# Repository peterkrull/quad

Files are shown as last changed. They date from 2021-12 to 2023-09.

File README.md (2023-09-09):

# Project quad

This git repository is a personal project of mine to develop an open-source autonomous quad copter using cheap off-the-shelf components in conjunction with control theory and state estimation. As much as possible, any auxiliary tools and documentation I produce, will also be a part of the repository.

## Getting Rusty

The [firmware](/software/rusty-quad) is written in the Rust programming language. This is in contrast to most flight controllers (and embedded devices in general) which use C or C++. The reason for choosing Rust is quite simple: it is a modern language. It can guarantee many things about the validity of memory at compile time, allows for writing high-level code, that runs at low-level speeds, and feels good to write; once you become friendly with the borrow checker.

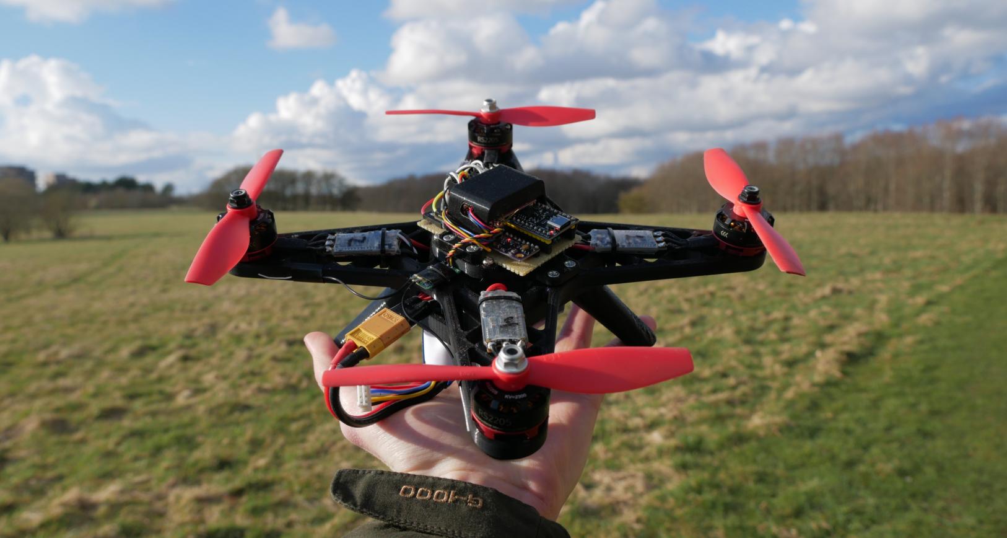
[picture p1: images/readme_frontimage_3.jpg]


### [*YouTube* : Demo of wireless data plotting and responsive controls](https://www.youtube.com/watch?v=jQ53PiUz8Us)

---

## Directory contents

- **[3dparts](/3dparts/)** - 3D models used in the project as STEP and .obj files.
- **[docs](/docs/)** - Documentation and learning material used in the project.
- **[hardware](/hardware/)** - Schematics, and PCB layouts as well as finished gerber files.
- **[images](/images/)** - Photos used in readme and some documentation.
- **[software](/software/)** - Software related to the project, including simulations, firmware, etc.
- **[tests](/tests/)** - Results from test conducted during this project

---

## Related repositories

During this project, some additional tools were developed, that reside in their own repositories.

### Rust crates

- [Async no-std ICM-20948 driver](https://github.com/peterkrull/icm20948-async)
- [Dshot driver for RP2040 PIO](https://github.com/peterkrull/dshot-pio)
- [Magnetometer calibration algorithm](https://github.com/peterkrull/mag-calibrator-rs)
- [Linear multi-sensor Kalman filter](https://github.com/peterkrull/kalman_filter_rust/)
- [(Forked) no-std SBUS-parser](https://github.com/peterkrull/sbus)

---

## License

This work is licensed under GPLv3.

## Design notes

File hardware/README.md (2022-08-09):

# Hardware

While a perfboard-based flight controller is fully capable, it is also heavy, large and labor intensive to manufacture. A compact and integrated PCB is a natural next step to reduce complexity, increase flexibility and reproducability.

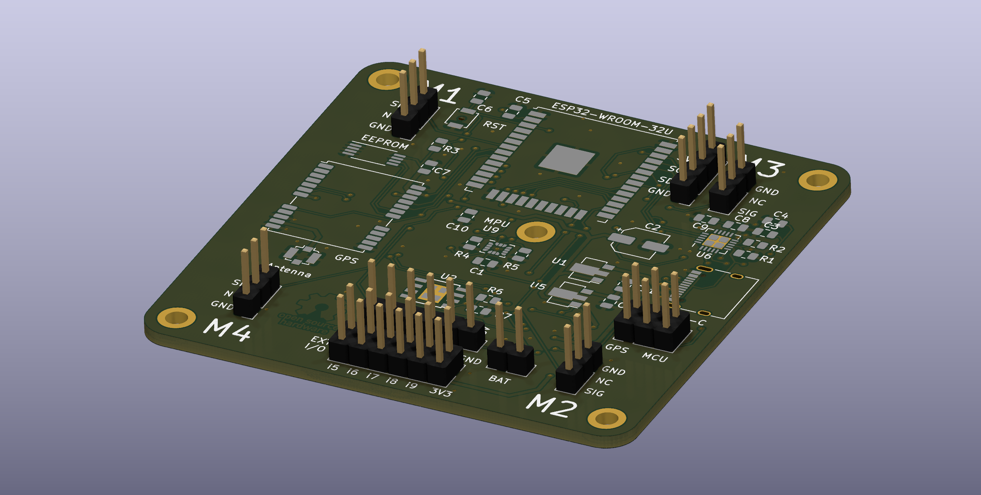
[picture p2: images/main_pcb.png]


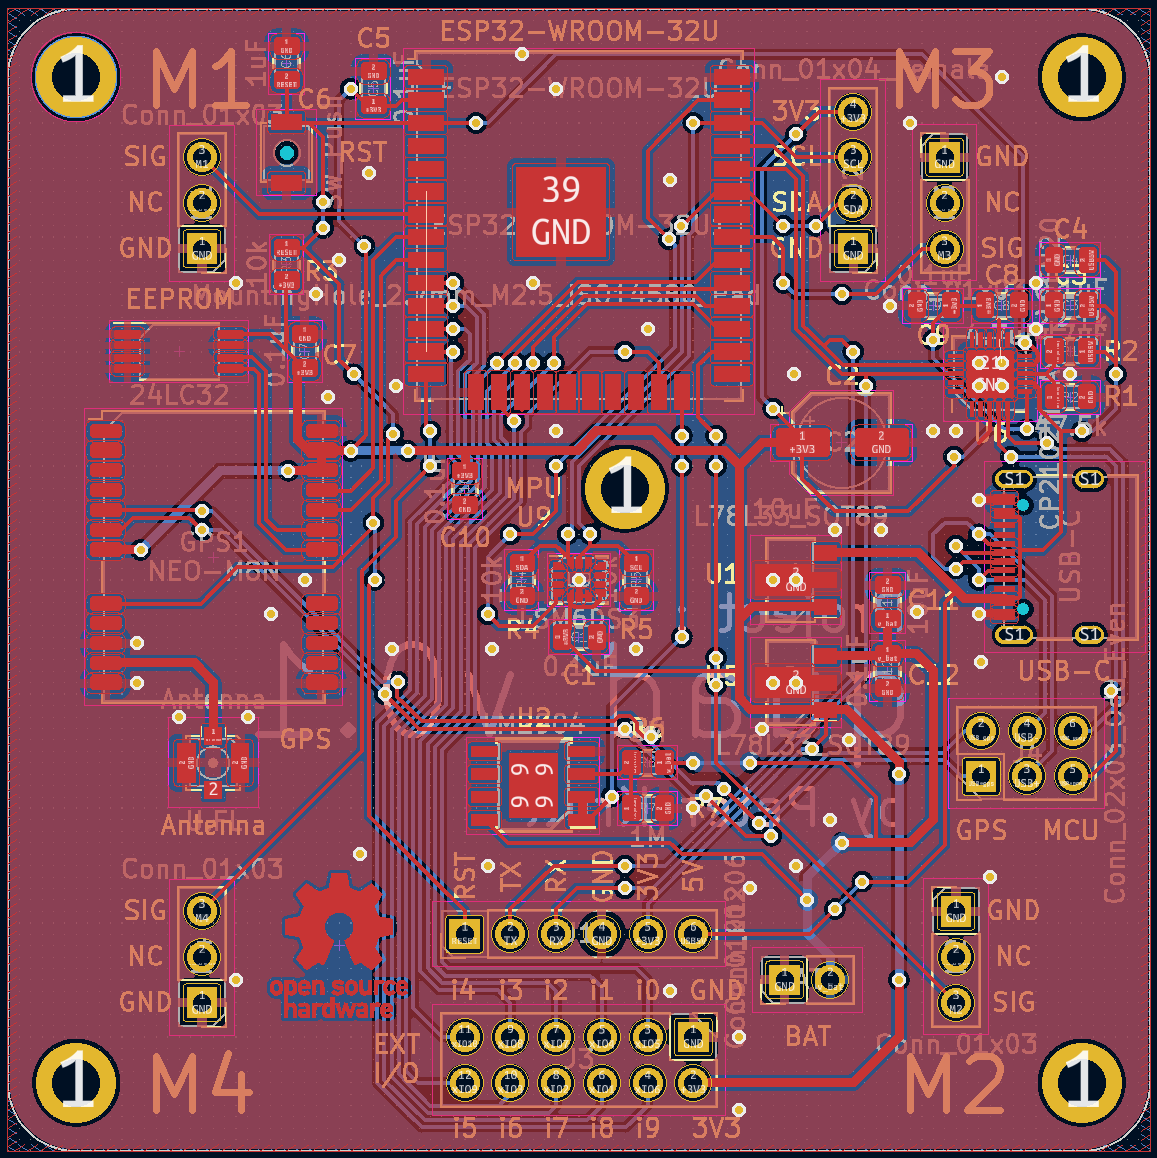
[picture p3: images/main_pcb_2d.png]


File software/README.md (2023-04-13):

# Software design

This directory contains first and foremost the Firmware developed for the drone, as well as any supporting software used for communication and data acquisition, processing, etc.

The rust-based flight controller can be found in
**[rusty-quad](/software/rusty-quad/)**

## Transition from C++ to Rust

The development of the firmware for the drone, has moved from an Arduino (C++) based framework, to Rust. The main micro-controller for development has also transitioned from the ESP32 platform, to the Raspberry Pi Pico (RP2040).

The rust-based firmware, unlike its C++ counterpart, has not yet proven air worthy, since some modules had to be written from scratch. This is due to embedded Rust still being in its infancy.

## Why Rust?

I started experimenting with Rust about a year ago, due to me finding its promises of memory safety, strict (yet somehow incredibly flexible) type system and C-like performance intriguing. On top of that, the modern tooling, package manager and passionate user base had me sold.

Equally intriguing to me, was the prospect of being able to develop micro-controller-embedded applications in Rust, with the amazing [**knurling-rs**](https://knurling.ferrous-systems.com/) tools by Ferrous Systems.

On top of that, Rust allows for high-speed, low overhead asynchronous programs using the built-in async/await syntax. For embedded applications, there is the [**Embassy**](https://github.com/embassy-rs/embassy) project specifically aimed at supporting async on embedded platforms.

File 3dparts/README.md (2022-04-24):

# 3D parts

This directory contains the 3D files designed for this project, both FreeCAD source files and 3D-printable .obj files.

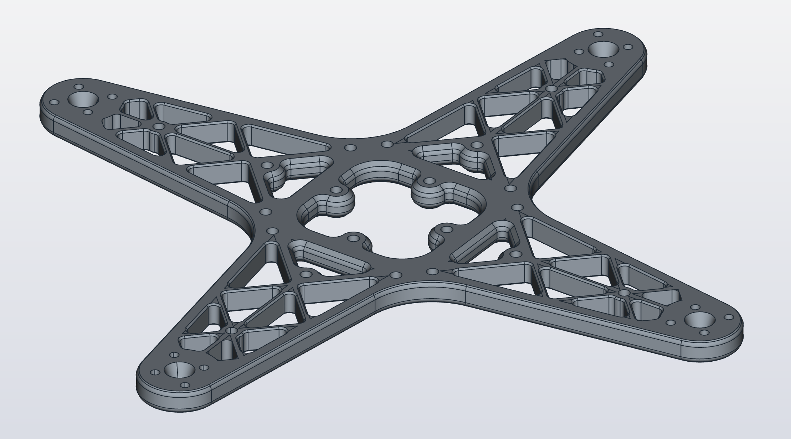
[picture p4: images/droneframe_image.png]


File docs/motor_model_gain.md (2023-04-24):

# Determining the motor model gain

Since the motor model is meant to relate the output thrust in newton to the input Dhsot command, the gain of the transfer function, or the constant in the numerator, is what defines this relation.

---

## Test setup and procedure

The thrust is measured in grams at 50 Hz using a strain gauge of the type [Eilersen SPSX](https://www.eilersen.com/single-point-load-cell/product/single-point-load-cell-spsx/) in combination with the [Eilersen 4X79A](https://www.eilersen.com/analog-weighing-module/product/analog-output-module-4x79a/) digital readout module, connected to a computer via ethernet, and read using a [program](/software/misc-tools/TCP_strain_guage.py) that establishes and logs a TCP data stream. A single motor with propeller is rigidly mounted to the strain gauge using [3D-printed parts](/3dparts/teststand_thrust/) and driven by a 30 A DShot ESC and a 4S Li-Po battery charged to 15.8 V.

---

## Results

Only one test was performed due to time constraints. The data collected using the TCP script mentioned above was imported and processed using a [Julia script](/tests/thrust_response/plotting_thrust_increaser.jl), where the data is converted to the correct units by scaling along both axes, then fitted to a first order polynomial, or a linear function. The resulting plot can be seen below.



Here we are only interested in the slope of the orange function, which is $4.436e-3$. This means that for the motor model, we have:

$$F(s)=\frac{4.436\cdot 10^{-3}}{\tau s + 1}$$

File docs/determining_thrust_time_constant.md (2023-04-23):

# Determining the time constant of a step in thrust

For this test, it is assumed that the thrust come-up of the motor + esc can be approximated as a first order model. Additionally, it is expected that the time constant is the same for any step-increase in thrust, just like the ideal motor model, but this will be verified during the test.

---

## Test setup and procedure

The thrust is measured in grams at 50 Hz using a strain gauge of the type [Eilersen SPSX](https://www.eilersen.com/single-point-load-cell/product/single-point-load-cell-spsx/) in combination with the [Eilersen 4X79A](https://www.eilersen.com/analog-weighing-module/product/analog-output-module-4x79a/) digital readout module, connected to a computer via ethernet, and read using a [program](/software/misc-tools/TCP_strain_guage.py) that establishes and logs a TCP data stream. A single motor with propeller is rigidly mounted to the strain gauge using [3D-printed parts](/3dparts/teststand_thrust/) and driven by a 30 A DShot ESC and a 4S Li-Po battery charged to 15.82 V.

---

## Results

Three tests were performed, where the motor went from a DShot command of 100 to [500](/tests/thrust_response/0500_thrust_response.csv), to [1200](/tests/thrust_response/1200_thrust_response.csv), and finally to [1500](/tests/thrust_response/1500_thrust_response.csv). These are analyzed using a [Julia script](/tests/thrust_response/plotting_thrust_steps.jl), where the step is set to happen at $t = 0$ as well as have steady-state gain of around $1$. An exponential function of the form $F(t)=1-e^{-\frac{t}{\tau}}$ is fitted to the data, where $\tau$ denotes the time constant of the first order system. It is determined for all three tests, that $\tau = 50 \text{ ms}$ is a good fit, striking a middle ground for any deviance there might be between them.



Using the same model in the laplace domain, we can describe the time constant of the motor model:

$$F(s) = \frac{G}{50\cdot 10^{-3}s + 1}$$

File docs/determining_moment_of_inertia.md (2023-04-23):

# Determining roll moment of inertia

The moment of inertia of some object is not always easy to measure. This is especially true if the object is of an odd size, shape and density. But if we are able to treat our object as a 'free body' where all quantities can be accounted for, then we can determine the moment of inertia by doing a test, where the change in angle over time is recorded when we apply a constant torque.

The moment of inertia is determined by applying a constant torque around the axis, and measuring the change in velocity over time. A constant torque can be accomplished using a known mass $M$ hanging by gravity $g$ from a string wound around a cylinder with radius $r$ giving : $\tau_t = M \cdot g \cdot r$. The moment of inertia $J$ can then be found by fitting the measurement to the following model:

A [3D-printed part](/3dparts/droneframe_v1/pitch_bearing_pivot_wide.obj) was designed specifically for this test, that is meant to replace the usual bearing holder for the pitch/roll test stand. This part has a diameter of $35 \text{ mm}$, so $r = (35/2)\cdot 10^{-3}$. Next, i used a roll of electrical tape, weighing $26 \text{ g}$, so $M = 26\cdot 10^{-3}$ and finally $g = 9.82$.

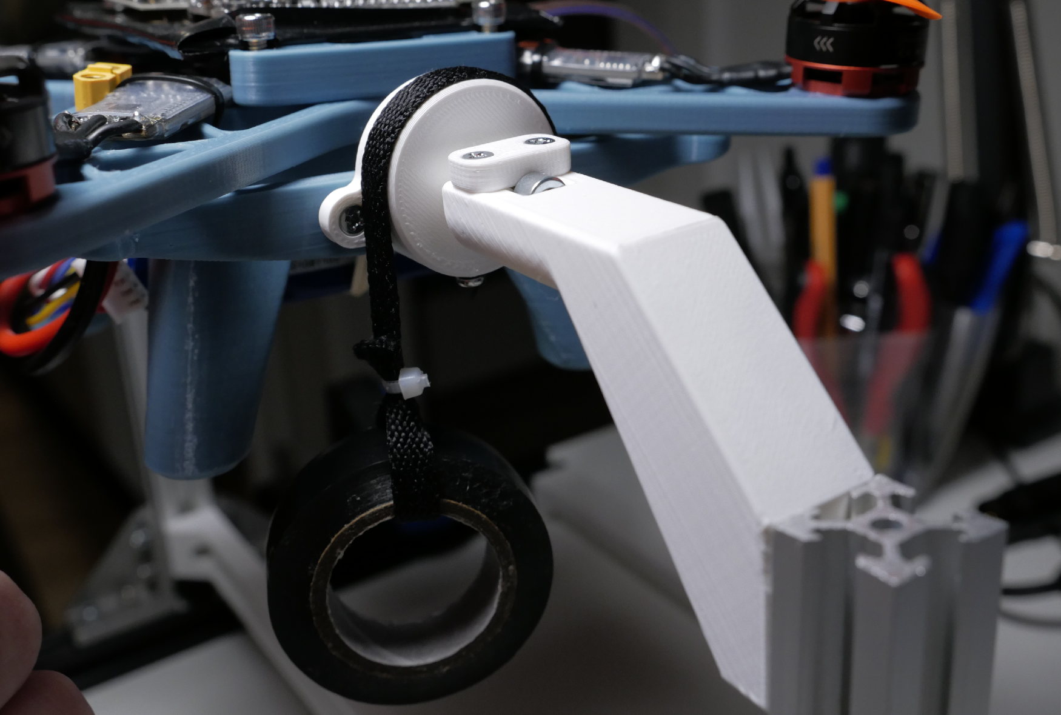
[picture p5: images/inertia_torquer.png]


For the test, a camera was mounted on a tripod recording in 4K with a fast shutter speed to prevent motion blur. Then, the drone was held at an angle to raise the roll of tape up high, and then let go. This is functionally a step in gravity and thus torque, that allows us to observe the change in angle over time. The video is processed in [Physlets tracker](https://physlets.org/tracker/) where two points are tracked on each opposing propeller. This gives us two sets of coordinates ([1](/tests/inertia_meas/pitch_inertia_left_point.csv) and [2](/tests/inertia_meas/pitch_inertia_right_point.csv)), where it is possible to determine the angle between them.

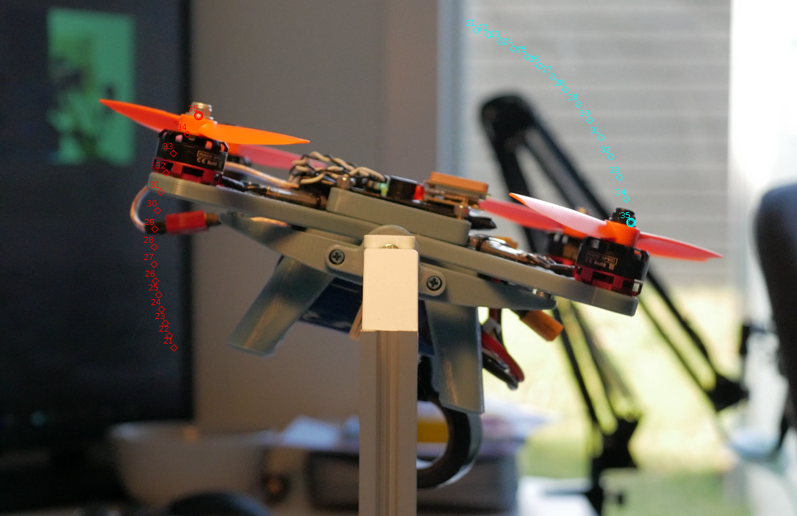
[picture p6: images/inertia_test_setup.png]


Finally, data processing!

A [Julia script](/tests/inertia_meas/roll_moment_inertia.jl) has been developed to calculate the angle using $\texttt{atan2}$, and angular velocity based on the timstamps from the video, as well as determine the moment of inertia that best fits the following transfer function, where some damping $B$ is expected:

$$\omega(s) = \frac{Mgr}{Js} \approx \frac{Mgr}{Js + B}$$

Both the moment of inertia, as well as the damping observed in the test were determined, though the dampening is of limited use at this point.
$$J = 1.2\cdot 10^{-3}$$
$$B = 0.4\cdot 10^{-3}$$



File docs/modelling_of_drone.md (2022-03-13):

# Modelling of drone

For any kind of control system, it is essential to have a good representation of the plant (the system to control) in order to determine the best strategy for control, as well as ensure system stability. For more complex systems, it can be beneficial to determine the transfer functions for smaller components in the system, and then combining them later on. This technique will be utilized here.

---

## Motors

The first critical element of quadcopter dynamics is the motor, propeller and motor controller. It is possible to measure each of these components characteristics individually, but as far as thrust is concerned they are essentially a SISO (single input, single output) system, thus may only be interested in the input/output characteristic. The measurement of step response and results of the motor, propeller and motor controller combo used for this project can be found in the [following document finding the time constant](/docs/determining_thrust_time_constant.md), in combination with [this document finding the gain](/docs/motor_model_gain.md) a first order transfer function can be determined of the form:

$$F(s) = \frac{G}{\tau s+1} \left[\frac{\text{N}}{\text{dshot}}\right]$$

Where $G$ is the steady-state relationship between input dshot command and thrust in newton around the operating point corresponding to a hover. We also have $\tau$ being the time constant of the first order system. The measurements resulted in the following transfer function:

$$F(s) = \frac{4.436\cdot10^{-3}}{50\cdot10^{-3}s+1}$$

---

## Equation of motion for pitch and roll

In [this document](/docs/equations_of_motion_pitch.md) the equation of motion for pitch and roll were determined

$$G(s)= \frac{2D}{Js+B} \left[\frac{\omega}{\text{N}}\right]$$

Where $D$ is the distance from the between two propellers, $J$ is the moment of inertial of the drone around the given axis, and $B$ is the air resistance. Here, $D$ is the only easily measureable constant. 

The moment of inertia is determined by applying a constant torque around the axis, and measuring the change in velocity over time. A constant torque can be accomplished using a known mass $M$ hanging by gravity $g$ from a string wound around a cylinder with radius $r$ giving : $\tau_t = M \cdot g \cdot r$. The moment of inertia $J$ can then be found by fitting the measurement to the following model:

$$\omega(s) = \frac{Mgr}{Js}$$

The value of $J$ for the pitch axis was found during the test described in [this document](/docs/determining_moment_of_inertia.md) to have a value of $1.2\cdot 10^{-3} \text{kg}/\text{m}^2$. A dampening constant $B$ was also found during the test, though this also included friction from the test setup, so the air resistance is approximated as half of this, resulting in the following transfer function for pitch:

$$G(s)= \frac{170\cdot 10^{-3}}{1.2\cdot 10^{-3}s+200\cdot 10^{-6}}$$

The moment of inertia for roll will not be explicitly measured, but it assumed to be $\approx 10$% lower due to the orientation of the battery.

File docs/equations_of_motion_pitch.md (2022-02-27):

# Pitch and roll - Equations of motion

In order to describe the relationship between the thrust of each motor and the roll behaviour, we can utilize a free-body diagram go get a better understanding of the elements at play and how they affect the system. Here we are interested in the mass moment of inertia of the drone, represented by $J$, the force provided by each motor $F_1,F_2,F_3,F_4$, the distance from the motor to the center of mass $R$, and finally the air resistance modelled as a pure dampener $B$

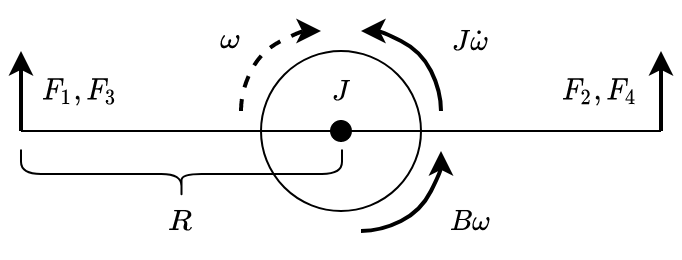
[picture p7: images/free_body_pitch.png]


Using this diagram, we can set up the following equations, considering the direction of rotation denoted by $\omega$.

$$J\dot{\omega} = F_2F_4R-F_1F_3R-B\omega$$

We bring it to the laplace domain:

$$J\omega(s)s = F_2(s)F_4(s)R-F_1(s)F_3(s)R-B\omega(s)$$

Next, we can simplify the motor forces. Since for a clockwise roll command, motors $F_1,F_3$ will increase in thrust, and motors $F_1,F_3$ will decrese with a similar, but negative amount of thrust, we can simplify to:

$$J\omega(s)s = 4F(s)R-B\omega(s)$$

We can now combine terms containing $\omega(s)$

$$\omega(s)(Js+B) = 4F(s)R$$

And finally cross-divide to get the transfer function. Since it might be easier to simply measure the distance between the center of two motors, we can define that $D = 2R$:

$$G(s)=\frac{\omega(s)}{F(s)} = \frac{4R}{(Js+B)} = \frac{2D}{(Js+B)}$$

This transfer function of the first order, due to the single $s$, resulting in a pole. It does assume that the propellers are a point source of thrust, and that they are on the exact same plane as the mass moment of inertia $J$. This might not be the case in reality, but the equation is likely to approximate the forces close enough.

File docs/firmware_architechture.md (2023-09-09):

# Firmware Architechture

This document seeks to describe the high-level design of the [flight controller](/software/rusty-quad/), written in Rust around the [Embassy](https://embassy.dev/) framework. This document will not go into depth with anything specific to the implementation (that is, no Rust code is shown), but the design will rely on some of the syncronization primitives provided by the Embassy framework.

## Message passing

The firmware makes great use of the async functionality provided by Embassy. This includes splitting the logic into a bunch of small self-contained programs, realized via Embassy `tasks`. The firmware therefore also relies heavily on message passing, usually via the `PubSubChannel` type, to allow for multiple receivers of the same message.

The firmware archtechture is described by the the diagram below.

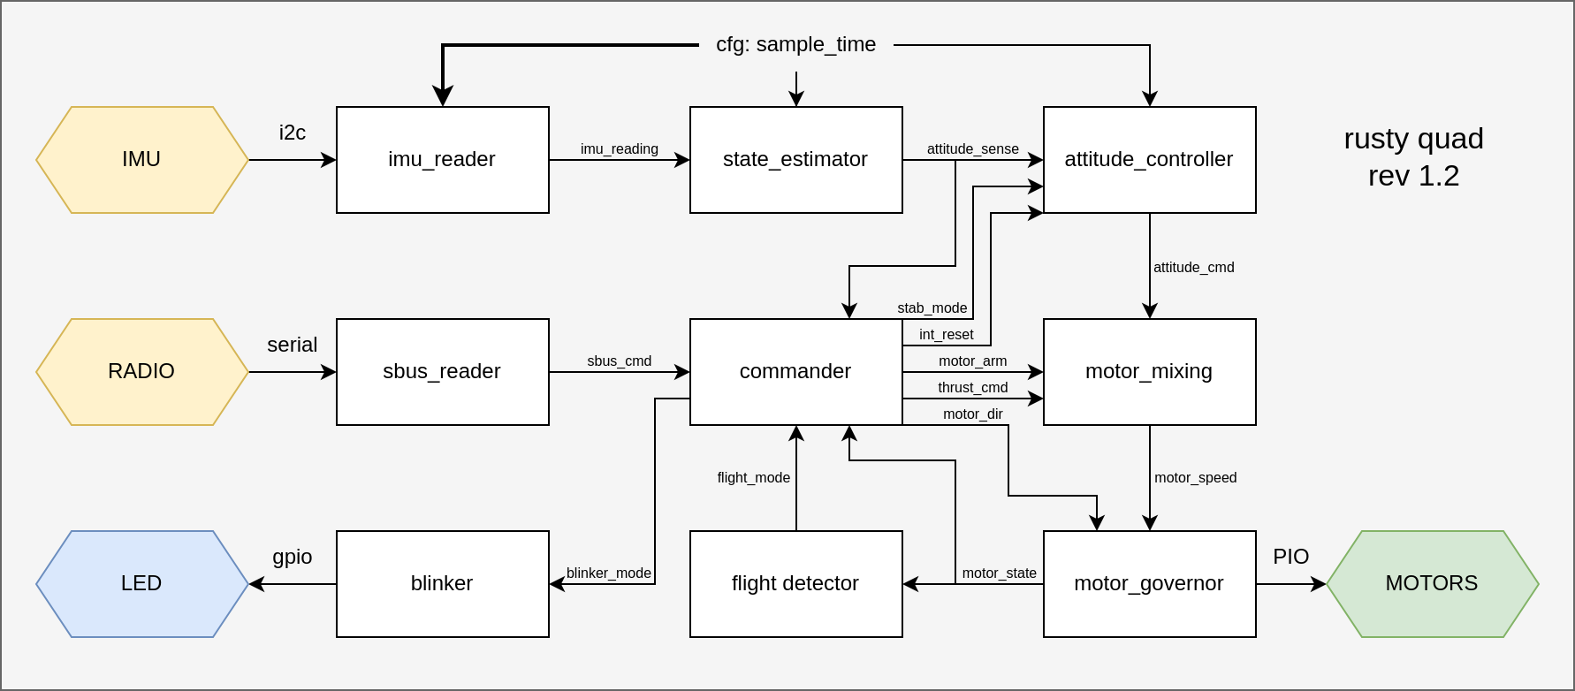
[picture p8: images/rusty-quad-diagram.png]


The architechture is arguably overkill given the current set of functionality, but it should *hopefully* make it easier to add more functionality down the road.

## Task signature structure

Each task signature must follow a clear set of rules, such that input/output relations are more easily reasoned. Take the example signature below. Inputs are clearly listed first, and outputs last. Additionally, the type of the signals are defined in a crate module called `signals`, such that everything relating to these signals, including the type of data and the number of receivers are contained in a single file.

```rust
use crate::signals;

#[embassy_executor::task]
pub async fn controller(
    in_enable:       signals::ConEnableSub,
    in_setpoint:     signals::ConSetpointSub,
    in_measurement:  signals::ConMeasurementSub,
    out_output:      signals::ConOutputPub,
) { ... }
```

The `PubSubChannel` channel type also allows for multiple senders, and queueing of data. These use cases are however not utilized in this project as of yet.

Each signal is defined by the number of receivers (subscribers), as well as the type of data within it. For example, the `ConEnableSub` signal from the example above could be defined like this.

```rust
const CON_ENABLE_NUM: usize = 1;
pub type ConEnableType = bool;
pub type ConEnablePub = Pub<ConEnableType,CON_ENABLE_NUM>;
pub type ConEnableSub = Sub<ConEnableType,CON_ENABLE_NUM>;
pub static CON_ENABLE : Ch<ConEnableType,CON_ENABLE_NUM> = PubSubChannel::new();
```

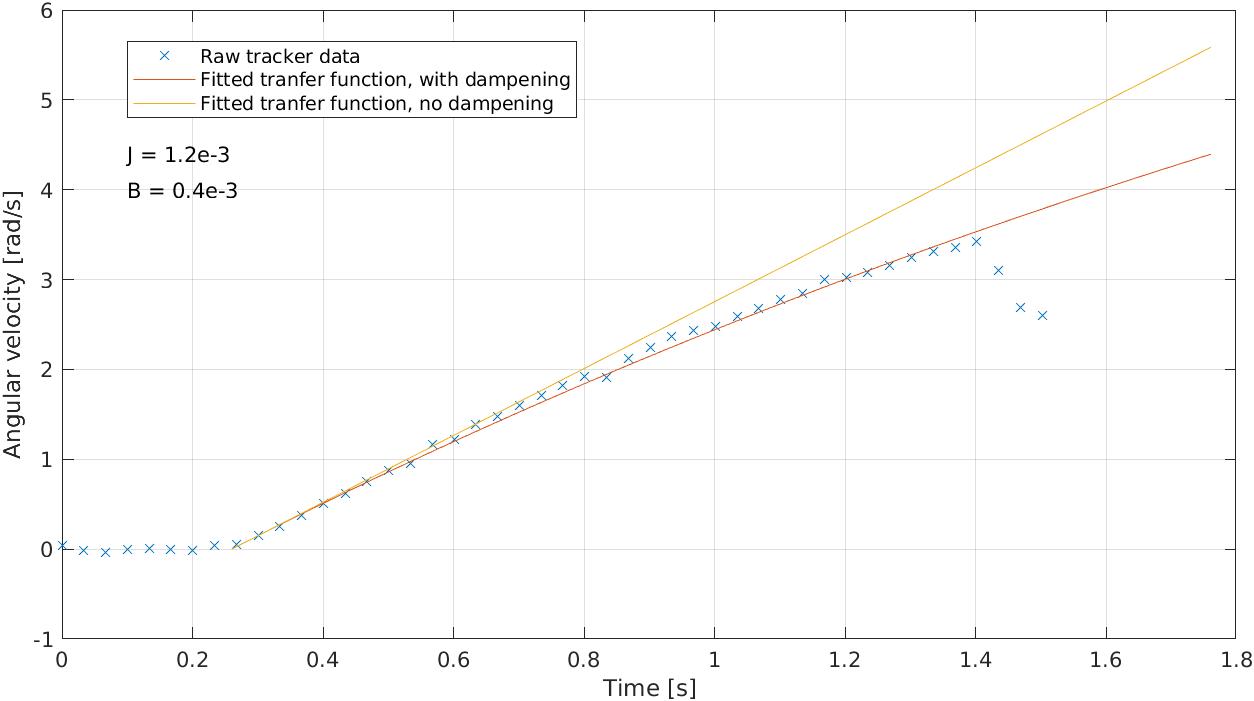
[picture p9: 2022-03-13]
images/roll_moment_of_inertia.jpg

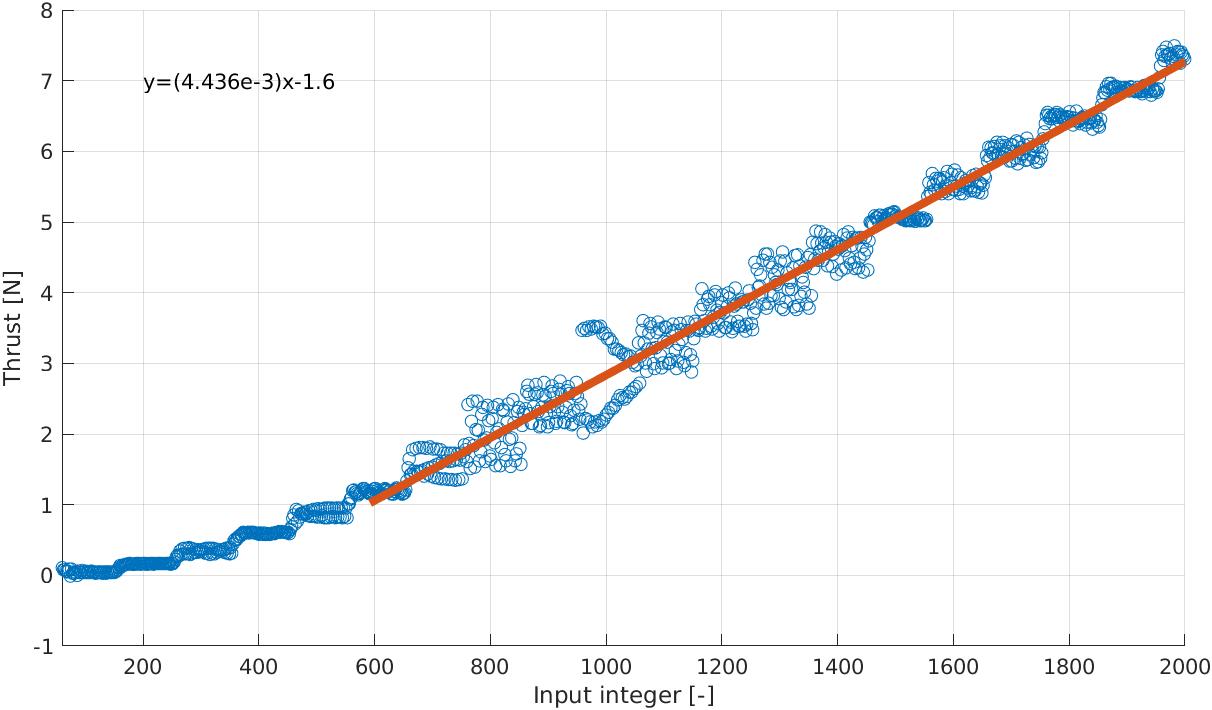
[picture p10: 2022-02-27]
images/thrust_linearization.jpg

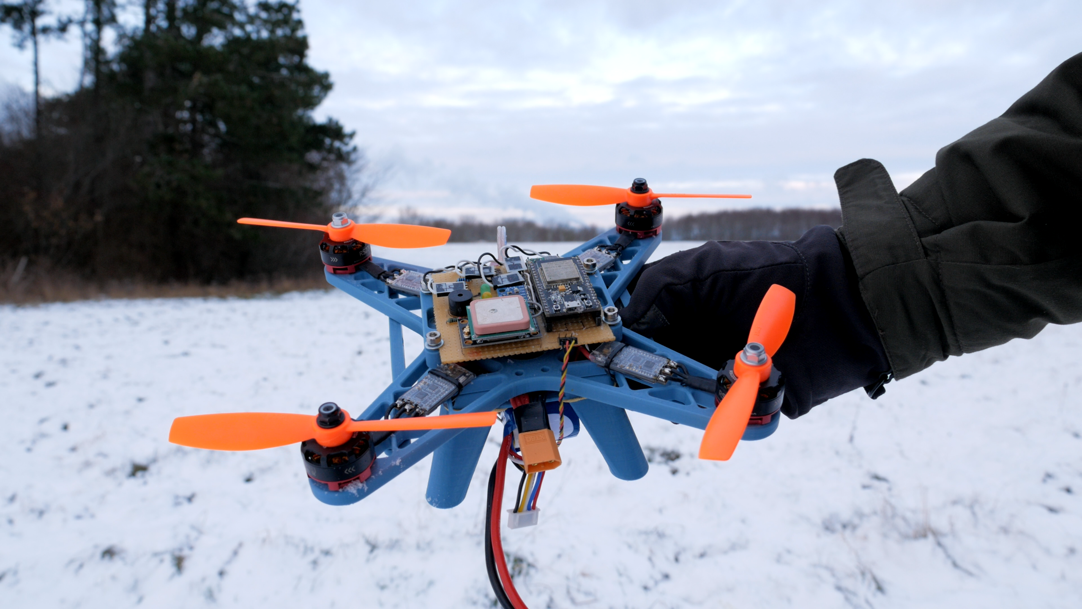
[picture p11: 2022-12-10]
images/readme_frontimage_2.png

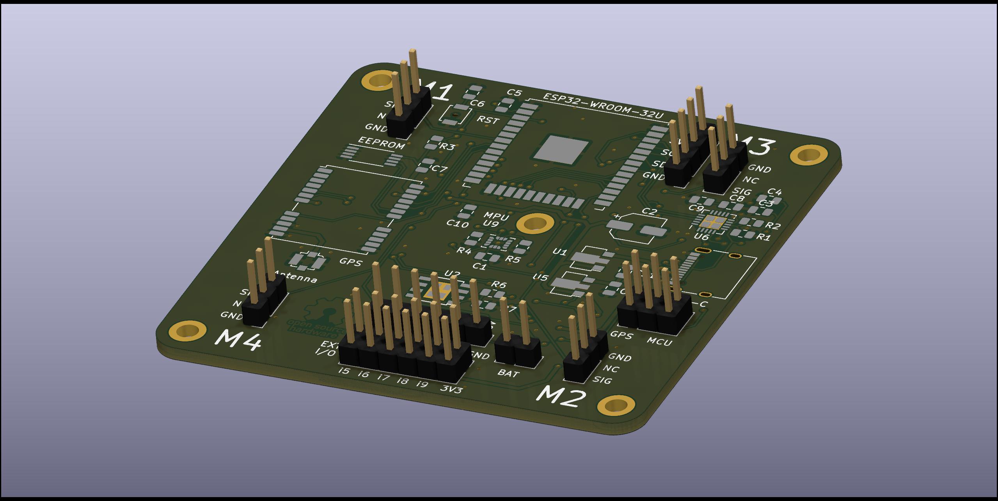
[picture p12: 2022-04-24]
images/main_pcb.jpg

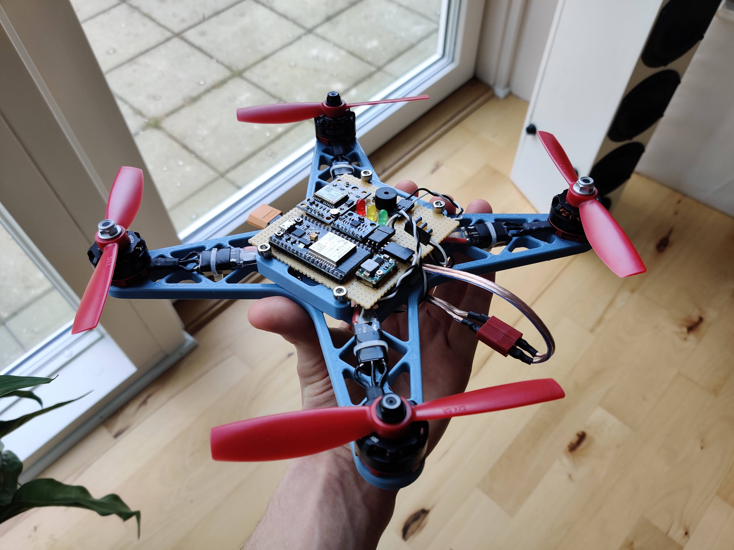
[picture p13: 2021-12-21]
images/readme_frontimage.jpg

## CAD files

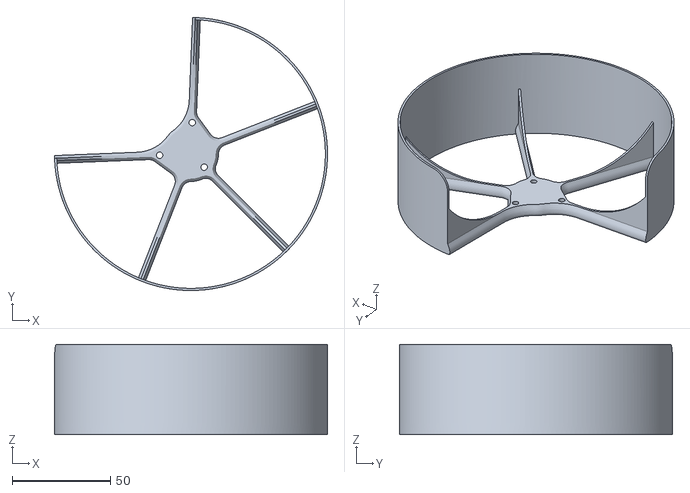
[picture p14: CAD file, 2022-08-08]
3dparts/droneframe_v1/droneframe_main_v1.1_propguard.obj
139.2 x 139.2 x 46.0

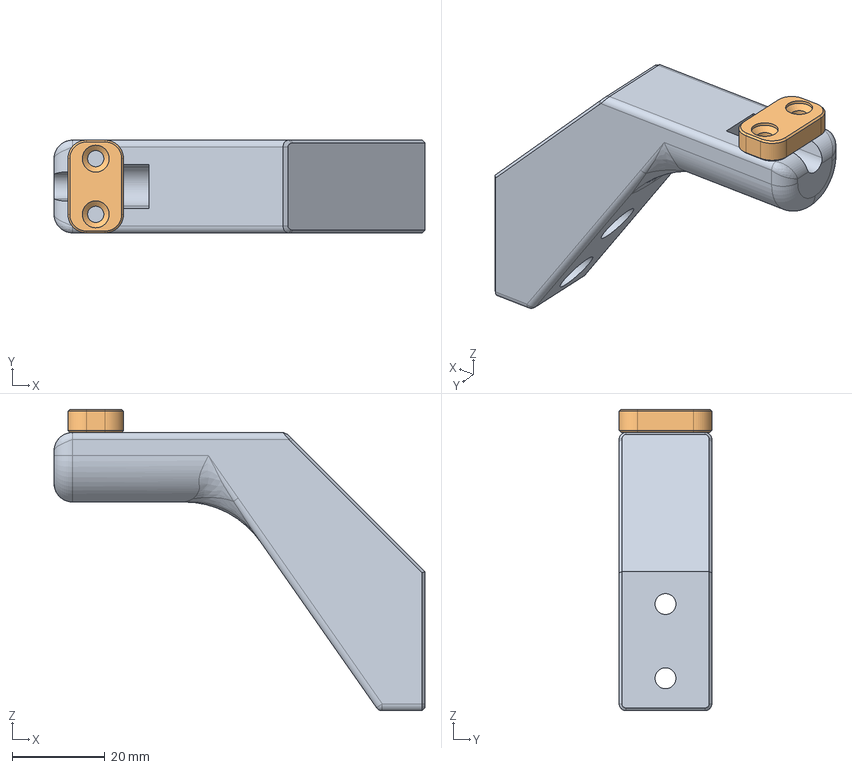
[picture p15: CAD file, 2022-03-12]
3dparts/teststand_pitch/swivel_point_32cm.FCStd
80.0 x 20.0 x 65.0 mm

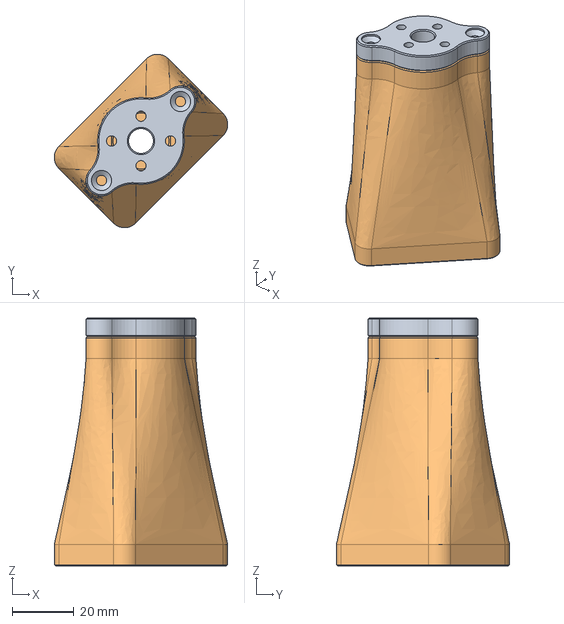
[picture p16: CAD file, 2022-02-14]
3dparts/teststand_thrust/thrust_mount.FCStd
55.9 x 55.9 x 80.0 mm

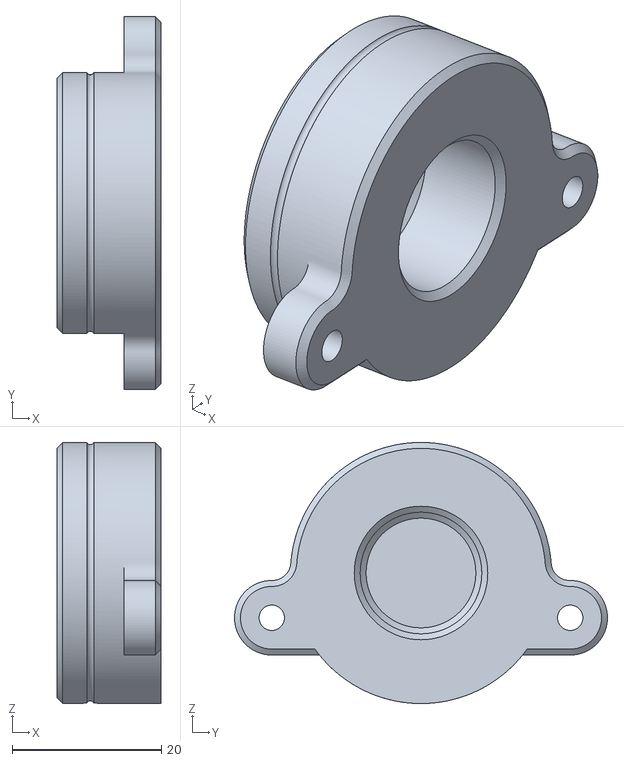
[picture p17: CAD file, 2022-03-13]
3dparts/droneframe_v1/pitch_bearing_pivot_wide.obj
14.0 x 50.0 x 35.0

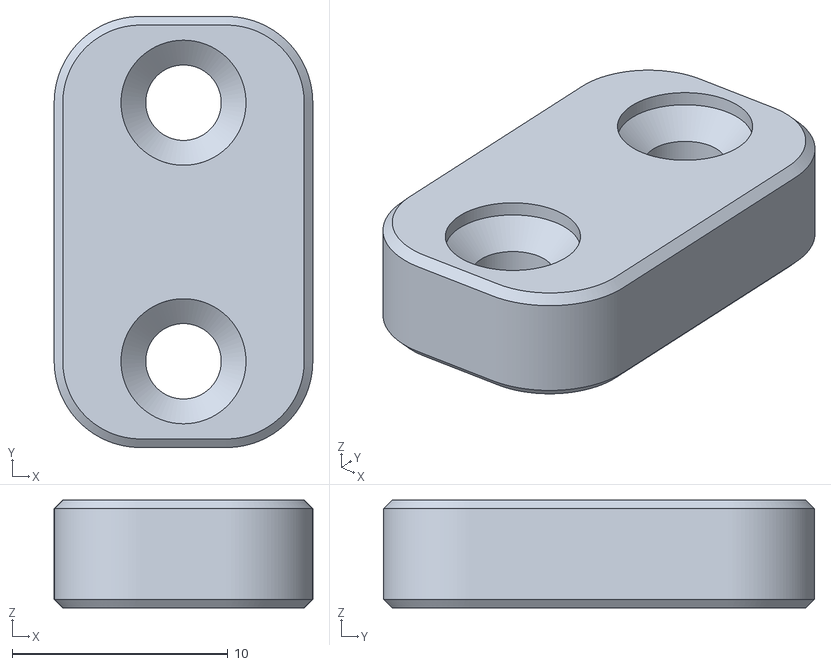
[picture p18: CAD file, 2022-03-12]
3dparts/teststand_pitch/swivel_point_32cm_clamp.obj
12.0 x 20.0 x 5.00

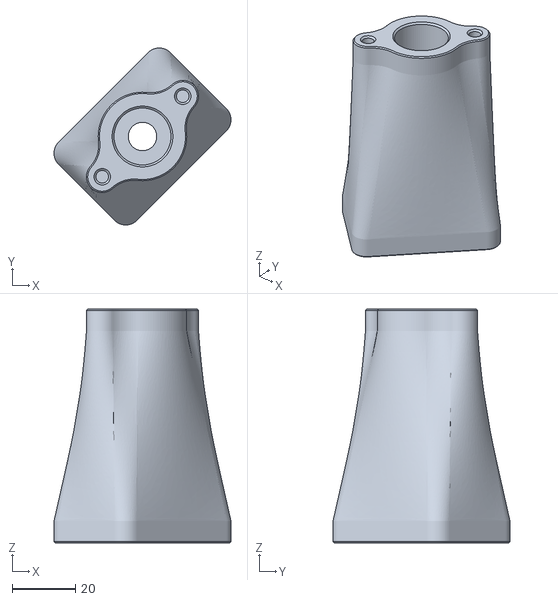
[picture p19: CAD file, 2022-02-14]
3dparts/teststand_thrust/thrust_mount_bottom.obj
56.0 x 56.0 x 74.0

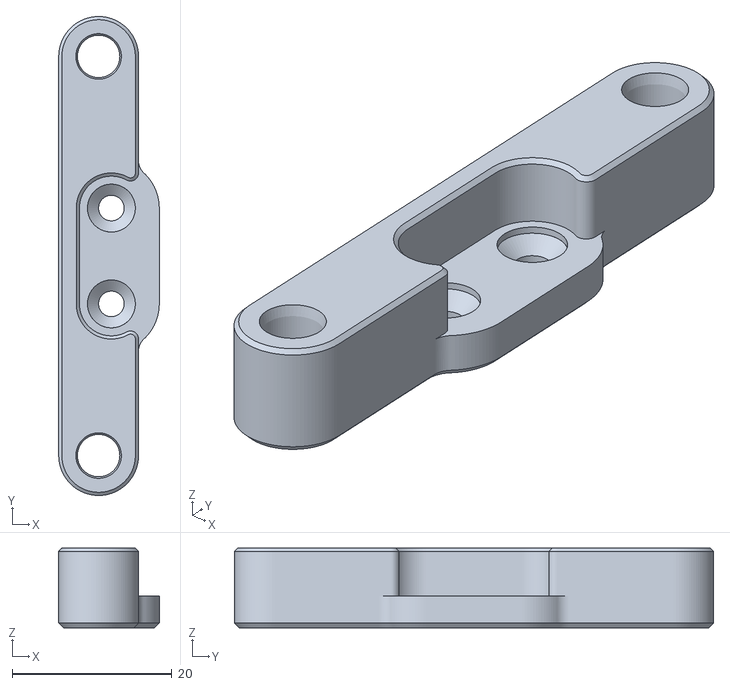
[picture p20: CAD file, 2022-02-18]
3dparts/droneframe_v1/droneframe_pcb_clamp_insert.obj
12.6 x 60.0 x 10.0

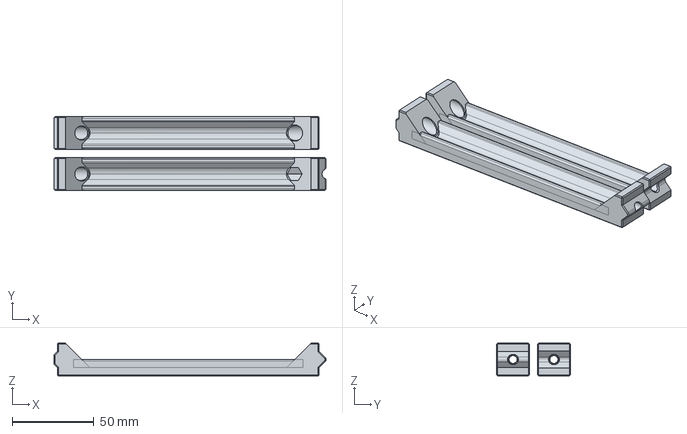
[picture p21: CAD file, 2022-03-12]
3dparts/teststand_pitch/32cm_spacer_pair.FCStd
166.2 x 45.0 x 20.0 mm

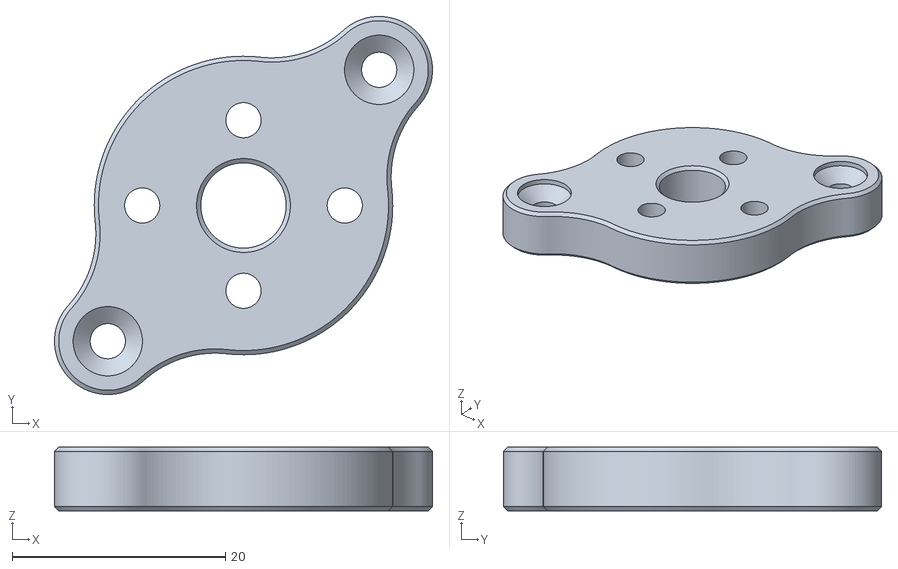
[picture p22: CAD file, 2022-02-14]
3dparts/teststand_thrust/thrust_mount_top.obj
35.5 x 35.5 x 6.00

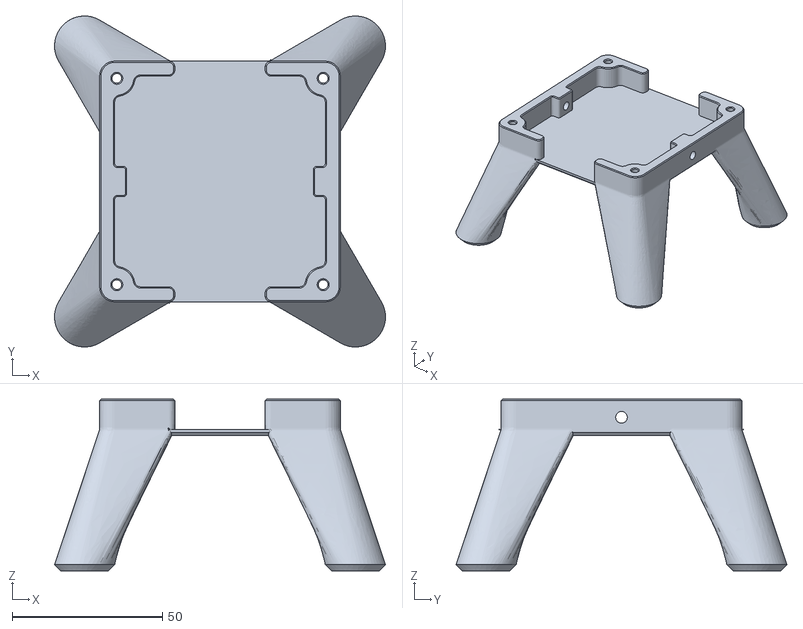
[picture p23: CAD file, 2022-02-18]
3dparts/droneframe_v1/landing_gear.obj
110.0 x 110.0 x 57.0

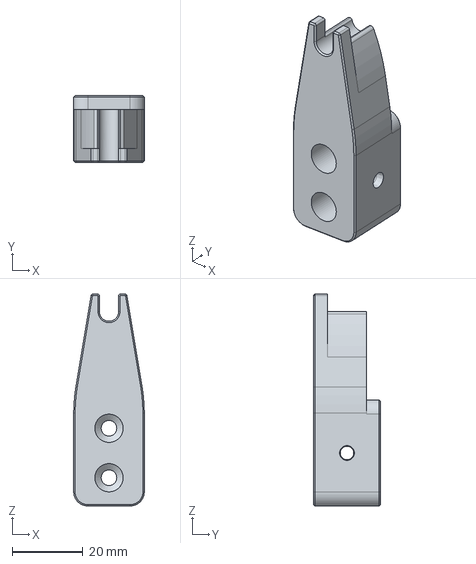
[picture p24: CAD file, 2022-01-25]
3dparts/teststand_pitch/swivel_point.FCStd
20.0 x 19.0 x 60.0 mm

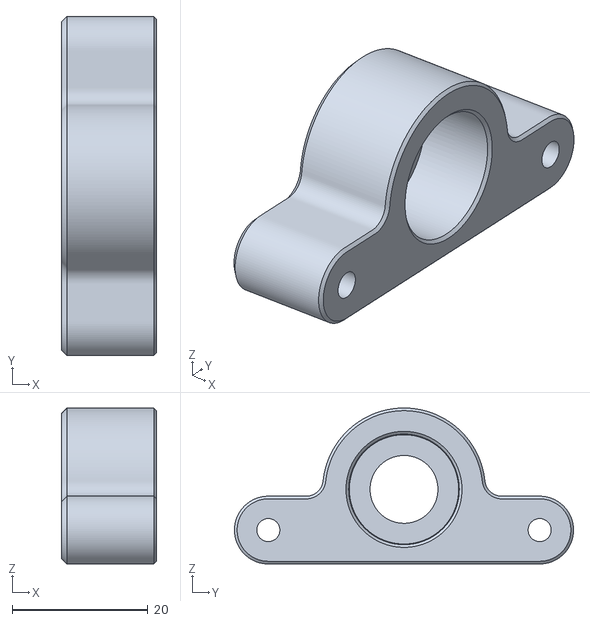
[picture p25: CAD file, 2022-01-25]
3dparts/droneframe_v1/pitch_bearing_pivot.obj
14.0 x 50.0 x 23.0

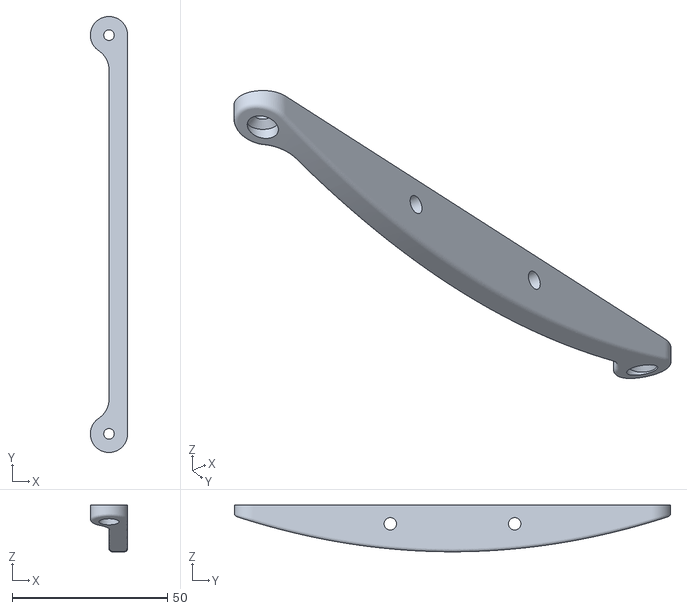
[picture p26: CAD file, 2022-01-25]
3dparts/droneframe_v1/pitch_spar.obj
12.0 x 140.3 x 15.0

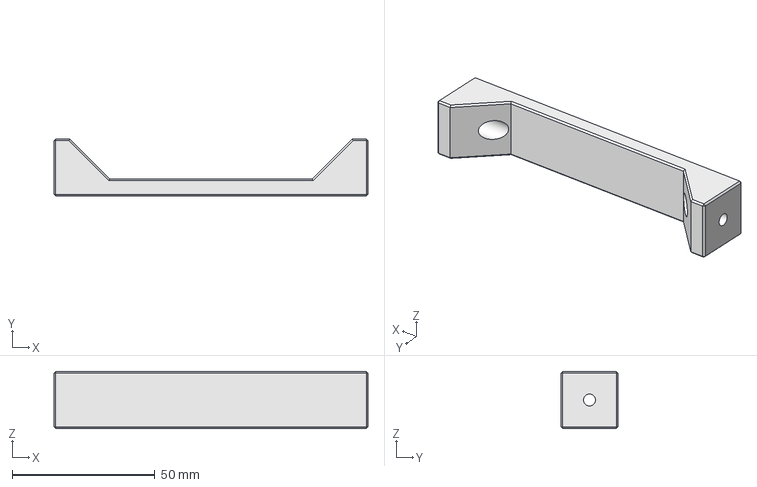
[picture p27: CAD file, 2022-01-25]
3dparts/teststand_pitch/11cm_spacer.FCStd
110.0 x 20.0 x 20.0 mm

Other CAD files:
3dparts/teststand_pitch/swivel_point-Body.obj
3dparts/droneframe_v1/droneframe_pcb_clamp.step
3dparts/droneframe_v1/droneframe_pcb_clamp.obj
3dparts/teststand_pitch/11cm_spacer.obj
3dparts/teststand_pitch/32cm_spacer_pair.obj
3dparts/teststand_pitch/swivel_point_32cm.obj

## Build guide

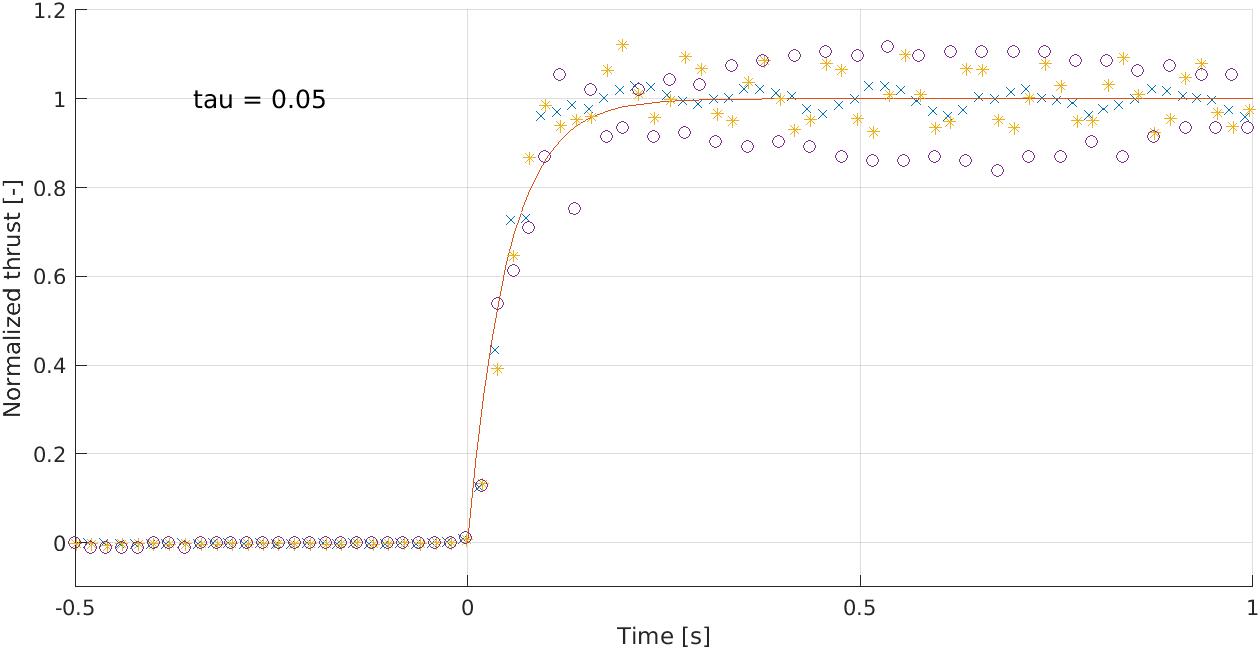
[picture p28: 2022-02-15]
images/thrust_step_plot.jpg

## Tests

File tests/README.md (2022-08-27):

# Tests
This readme is temporarily empty

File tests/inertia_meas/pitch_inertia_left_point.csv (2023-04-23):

t | x | y
0.000000000E0 | 1.394885864E-1 | -1.726483102E-1
3.336666667E-2 | 1.393390014E-1 | -1.725067125E-1
6.673333333E-2 | 1.393999060E-1 | -1.726566626E-1
1.001000000E-1 | 1.394419151E-1 | -1.726658692E-1
1.334666667E-1 | 1.394240809E-1 | -1.727590122E-1
1.668333333E-1 | 1.393678600E-1 | -1.726344655E-1
2.002000000E-1 | 1.394195811E-1 | -1.726922569E-1
2.335666667E-1 | 1.394881270E-1 | -1.726808607E-1
2.669333333E-1 | 1.393665015E-1 | -1.725007581E-1
3.003000000E-1 | 1.392822858E-1 | -1.724968283E-1
3.336666667E-1 | 1.389010537E-1 | -1.720086276E-1
3.670333333E-1 | 1.382463759E-1 | -1.714128393E-1
4.004000000E-1 | 1.375130576E-1 | -1.705127215E-1
4.337666667E-1 | 1.364832390E-1 | -1.691292813E-1
4.671333333E-1 | 1.352677842E-1 | -1.675763259E-1
5.005000000E-1 | 1.338354463E-1 | -1.656905891E-1
5.338666667E-1 | 1.322761334E-1 | -1.633891591E-1
5.672333333E-1 | 1.305954636E-1 | -1.607906878E-1
6.006000000E-1 | 1.287884337E-1 | -1.578290970E-1
6.339666667E-1 | 1.269838250E-1 | -1.544757825E-1
6.673333333E-1 | 1.250555359E-1 | -1.506150541E-1
7.007000000E-1 | 1.232481184E-1 | -1.464893386E-1
7.340666667E-1 | 1.214488217E-1 | -1.419744128E-1
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

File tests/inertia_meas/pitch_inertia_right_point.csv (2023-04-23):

t | x | y
0.000000000E0 | 2.118200548E-1 | -1.652707486E-2
3.336666667E-2 | 2.117939632E-1 | -1.665349951E-2
6.673333333E-2 | 2.119328405E-1 | -1.647661908E-2
1.001000000E-1 | 2.117182821E-1 | -1.651242696E-2
1.334666667E-1 | 2.117648524E-1 | -1.647213592E-2
1.668333333E-1 | 2.116853645E-1 | -1.646732020E-2
2.002000000E-1 | 2.117536479E-1 | -1.644460465E-2
2.335666667E-1 | 2.116523428E-1 | -1.652501259E-2
2.669333333E-1 | 2.117119906E-1 | -1.644422995E-2
3.003000000E-1 | 2.118912852E-1 | -1.661758525E-2
3.336666667E-1 | 2.122905488E-1 | -1.658508615E-2
3.670333333E-1 | 2.129459591E-1 | -1.663910590E-2
4.004000000E-1 | 2.141124153E-1 | -1.667929022E-2
4.337666667E-1 | 2.156176585E-1 | -1.675434140E-2
4.671333333E-1 | 2.174993625E-1 | -1.694060057E-2
5.005000000E-1 | 2.198135078E-1 | -1.719543174E-2
5.338666667E-1 | 2.223613958E-1 | -1.776663233E-2
5.672333333E-1 | 2.251747301E-1 | -1.822699612E-2
6.006000000E-1 | 2.287079828E-1 | -1.924700557E-2
6.339666667E-1 | 2.324349385E-1 | -2.014153759E-2
6.673333333E-1 | 2.365134748E-1 | -2.142478377E-2
7.007000000E-1 | 2.409241531E-1 | -2.299288440E-2
7.340666667E-1 | 2.455690809E-1 | -2.490210979E-2
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

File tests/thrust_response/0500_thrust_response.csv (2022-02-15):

4.0531158447265625e-06 | 0.793
0.020004053115844727 | 0.796
0.04000405311584473 | 0.795
0.054398298263549805 | 0.794
0.07439829826354981 | 0.796
0.09439829826354981 | 0.795
0.11413288116455078 | 0.795
0.13413288116455077 | 0.795
0.1541328811645508 | 0.795
0.17373299598693848 | 0.795
0.19373299598693847 | 0.796
0.21373299598693848 | 0.795
0.23326826095581055 | 0.795
0.25326826095581056 | 0.796
0.2732682609558105 | 0.795
0.2936062812805176 | 0.795
0.3136062812805176 | 0.796
0.33360628128051756 | 0.795
0.3523097038269043 | 0.796
0.3723097038269043 | 0.795
0.3923097038269043 | 0.795
0.41237545013427734 | 0.796
0.43237545013427736 | 0.795
0.4523754501342773 | 0.795
0.47281908988952637 | 0.796
0.4928190898895264 | 0.795
0.5128190898895264 | 0.795
0.5321133136749268 | 0.796
0.5521133136749268 | 0.796
0.5721133136749268 | 0.796
0.5916707515716553 | 0.795
0.6116707515716553 | 0.796
0.6316707515716553 | 0.796
0.651252031326294 | 0.795
0.671252031326294 | 0.796
0.691252031326294 | 0.796
0.7112417221069336 | 0.795
0.7312417221069336 | 0.795
0.7512417221069336 | 0.796
0.7718188762664795 | 0.796
0.7918188762664795 | 0.796
0.8118188762664795 | 0.794
0.8303976058959961 | 0.795
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

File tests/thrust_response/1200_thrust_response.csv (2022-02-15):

2.1457672119140625e-06 | 0.797
0.020002145767211914 | 0.797
0.040002145767211915 | 0.796
0.05226302146911621 | 0.797
0.07226302146911621 | 0.796
0.09226302146911622 | 0.797
0.11225461959838867 | 0.797
0.13225461959838866 | 0.796
0.15225461959838868 | 0.796
0.17280817031860352 | 0.796
0.1928081703186035 | 0.798
0.21280817031860352 | 0.796
0.2322545051574707 | 0.796
0.2522545051574707 | 0.797
0.2722545051574707 | 0.796
0.29180026054382324 | 0.797
0.31180026054382326 | 0.797
0.3318002605438232 | 0.795
0.35132455825805664 | 0.797
0.37132455825805666 | 0.797
0.3913245582580566 | 0.796
0.41135120391845703 | 0.797
0.43135120391845705 | 0.797
0.451351203918457 | 0.796
0.47066712379455566 | 0.797
0.4906671237945557 | 0.797
0.5106671237945557 | 0.796
0.5302457809448242 | 0.797
0.5502457809448242 | 0.797
0.5702457809448243 | 0.796
0.5906758308410645 | 0.797
0.6106758308410645 | 0.796
0.6306758308410645 | 0.797
0.6502737998962402 | 0.797
0.6702737998962403 | 0.796
0.6902737998962403 | 0.797
0.7093520164489746 | 0.796
0.7293520164489746 | 0.796
0.7493520164489746 | 0.797
0.769892692565918 | 0.797
0.789892692565918 | 0.796
0.809892692565918 | 0.797
0.8292961120605469 | 0.796
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

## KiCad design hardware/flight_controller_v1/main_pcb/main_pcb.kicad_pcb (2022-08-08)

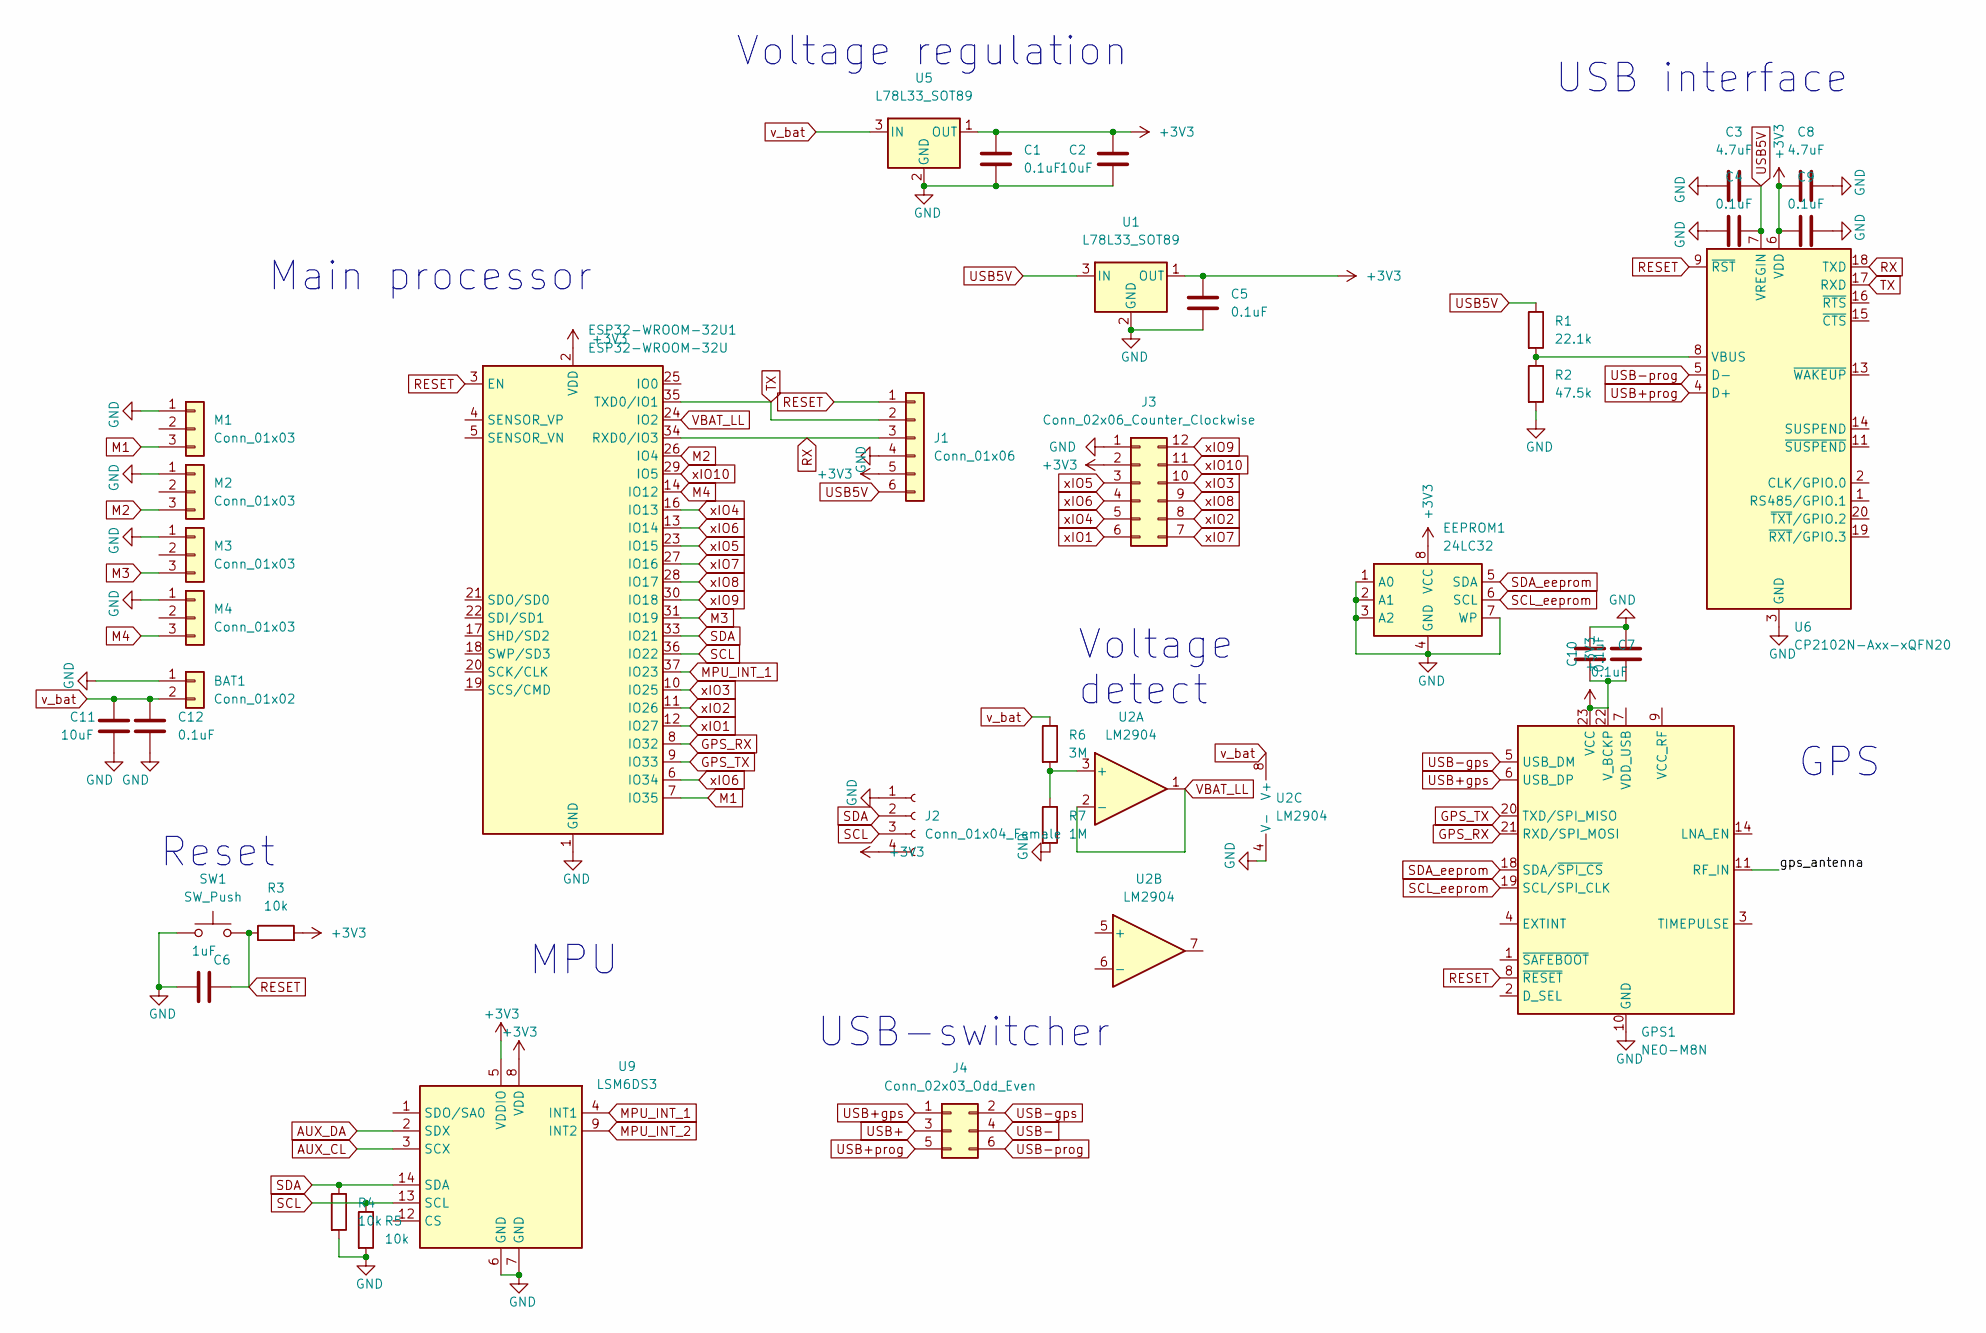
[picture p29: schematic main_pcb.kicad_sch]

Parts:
BAT1: Conn_01x02; PinHeader_1x02_P2.54mm_Vertical
C1, C4, C5, C7, C9, C10, C12: 0.1uF; C_0805_2012Metric
C2: 10uF; CP_Elec_5x4.5
C3, C8: 4.7uF; C_0805_2012Metric
C6: 1uF; C_0805_2012Metric
C11: 10uF; C_0805_2012Metric
EEPROM1: 24LC32; TSSOP-8_4.4x3mm_P0.65mm
ESP32-WROOM-32U1: ESP32-WROOM-32U
GPS1: NEO-M8N; ublox_NEO
J1: Conn_01x06; PinHeader_1x06_P2.54mm_Vertical
J2: Conn_01x04_Female; PinHeader_1x04_P2.54mm_Vertical
J3: Conn_02x06_Counter_Clockwise; PinHeader_2x06_P2.54mm_Vertical
J4: Conn_02x03_Odd_Even; PinHeader_2x03_P2.54mm_Vertical
M1, M2, M3, M4: Conn_01x03; PinHeader_1x03_P2.54mm_Vertical
R1: 22.1k; R_0805_2012Metric
R2: 47.5k; R_0805_2012Metric
R3, R4, R5: 10k; R_0805_2012Metric
R6: 3M; R_0805_2012Metric
R7: 1M; R_0805_2012Metric
SW1: SW_Push; SW_SPST_B3U-1000P-B
U1, U5: L78L33_SOT89; SOT-89-3
U2: LM2904; Diodes_PSOP-8
U6: CP2102N-Axx-xQFN20; MLF-20-1EP_4x4mm_P0.5mm_EP2.6x2.6mm
U9: LSM6DS3; LGA-14_3x2.5mm_P0.5mm_LayoutBorder3x4y

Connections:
+3V3: C1.1, C2.1, C5.1, C7.2, C8.1, C9.1, C10.1, EEPROM1.8 (VCC), ESP32-WROOM-32U1.2 (VDD), GPS1.22 (V_BCKP), GPS1.23 (VCC), J1.5, J2.4, J3.2, R3.2, U1.1 (OUT), U5.1 (OUT), U6.6 (VDD), U9.5 (VDDIO), U9.8 (VDD)
/gps_antenna: GPS1.11 (RF_IN); also elsewhere on the board
AUX_CL: U9.3 (SCX)
AUX_DA: U9.2 (SDX)
GND: BAT1.1, C1.2, C2.2, C3.1, C4.1, C5.2, C6.1, C7.1, C8.2, C9.2, C10.2, C11.2, C12.2, EEPROM1.1 (A0), EEPROM1.2 (A1), EEPROM1.3 (A2), EEPROM1.4 (GND), EEPROM1.7 (WP), ESP32-WROOM-32U1.1 (GND), ESP32-WROOM-32U1.15 (GND), ESP32-WROOM-32U1.38 (GND), ESP32-WROOM-32U1.39 (GND), GPS1.10 (GND), GPS1.12 (GND), GPS1.13 (GND), GPS1.24 (GND), J1.4, J2.1, J3.1, M1.1, M2.1, M3.1, M4.1, R2.2, R4.2, R5.2, R7.2, SW1.1, U1.2 (GND), U2.4 (V-), U5.2 (GND), U6.3 (GND), U6.12 (GND), U6.21 (GND), U9.6 (GND), U9.7 (GND); also elsewhere on the board
GPS_RX: ESP32-WROOM-32U1.8 (IO32), GPS1.21 (RXD/SPI_MOSI)
GPS_TX: ESP32-WROOM-32U1.9 (IO33), GPS1.20 (TXD/SPI_MISO)
M1: ESP32-WROOM-32U1.7 (IO35), M1.3
M2: ESP32-WROOM-32U1.26 (IO4), M2.3
M3: ESP32-WROOM-32U1.31 (IO19), M3.3
M4: ESP32-WROOM-32U1.14 (IO12), M4.3
MPU_INT_1: ESP32-WROOM-32U1.37 (IO23), U9.4 (INT1)
MPU_INT_2: U9.9 (INT2)
unnamed: R1.2, R2.1, U6.8 (VBUS)
unnamed: R6.2, R7.1, U2.3 (+)
RESET: C6.2, ESP32-WROOM-32U1.3 (EN), GPS1.8 (~RESET), J1.1, R3.1, SW1.2, U6.9 (~RST)
RX: ESP32-WROOM-32U1.34 (RXD0/IO3), J1.3, U6.18 (TXD)
SCL: ESP32-WROOM-32U1.36 (IO22), J2.3, R5.1, U9.13 (SCL)
SCL_eeprom: EEPROM1.6 (SCL), GPS1.19 (SCL/SPI_CLK)
SDA: ESP32-WROOM-32U1.33 (IO21), J2.2, R4.1, U9.14 (SDA)
SDA_eeprom: EEPROM1.5 (SDA), GPS1.18 (SDA/~SPI_CS)
TX: ESP32-WROOM-32U1.35 (TXD0/IO1), J1.2, U6.17 (RXD)
USB5V: C3.2, C4.2, J1.6, R1.1, U1.3 (IN), U6.7 (VREGIN); also elsewhere on the board
USB+: J4.3; also elsewhere on the board
USB+gps: GPS1.6 (USB_DP), J4.1
USB+prog: J4.5, U6.4 (D+)
USB-: J4.4; also elsewhere on the board
USB-gps: GPS1.5 (USB_DM), J4.2
USB-prog: J4.6, U6.5 (D-)
VBAT_LL: ESP32-WROOM-32U1.24 (IO2), U2.1, U2.2 (-)
v_bat: BAT1.2, C11.1, C12.1, R6.1, U2.8 (V+), U5.3 (IN)
xIO1: ESP32-WROOM-32U1.12 (IO27), J3.6
xIO2: ESP32-WROOM-32U1.11 (IO26), J3.8
xIO3: ESP32-WROOM-32U1.10 (IO25), J3.10
xIO4: ESP32-WROOM-32U1.16 (IO13), J3.5
xIO5: ESP32-WROOM-32U1.23 (IO15), J3.3
xIO6: ESP32-WROOM-32U1.6 (IO34), ESP32-WROOM-32U1.13 (IO14), J3.4
xIO7: ESP32-WROOM-32U1.27 (IO16), J3.7
xIO8: ESP32-WROOM-32U1.28 (IO17), J3.9
xIO9: ESP32-WROOM-32U1.30 (IO18), J3.12
xIO10: ESP32-WROOM-32U1.29 (IO5), J3.11

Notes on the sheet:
Voltage detect
USB-switcher
Reset
GPS
MPU
Main processor
Voltage regulation
USB interface

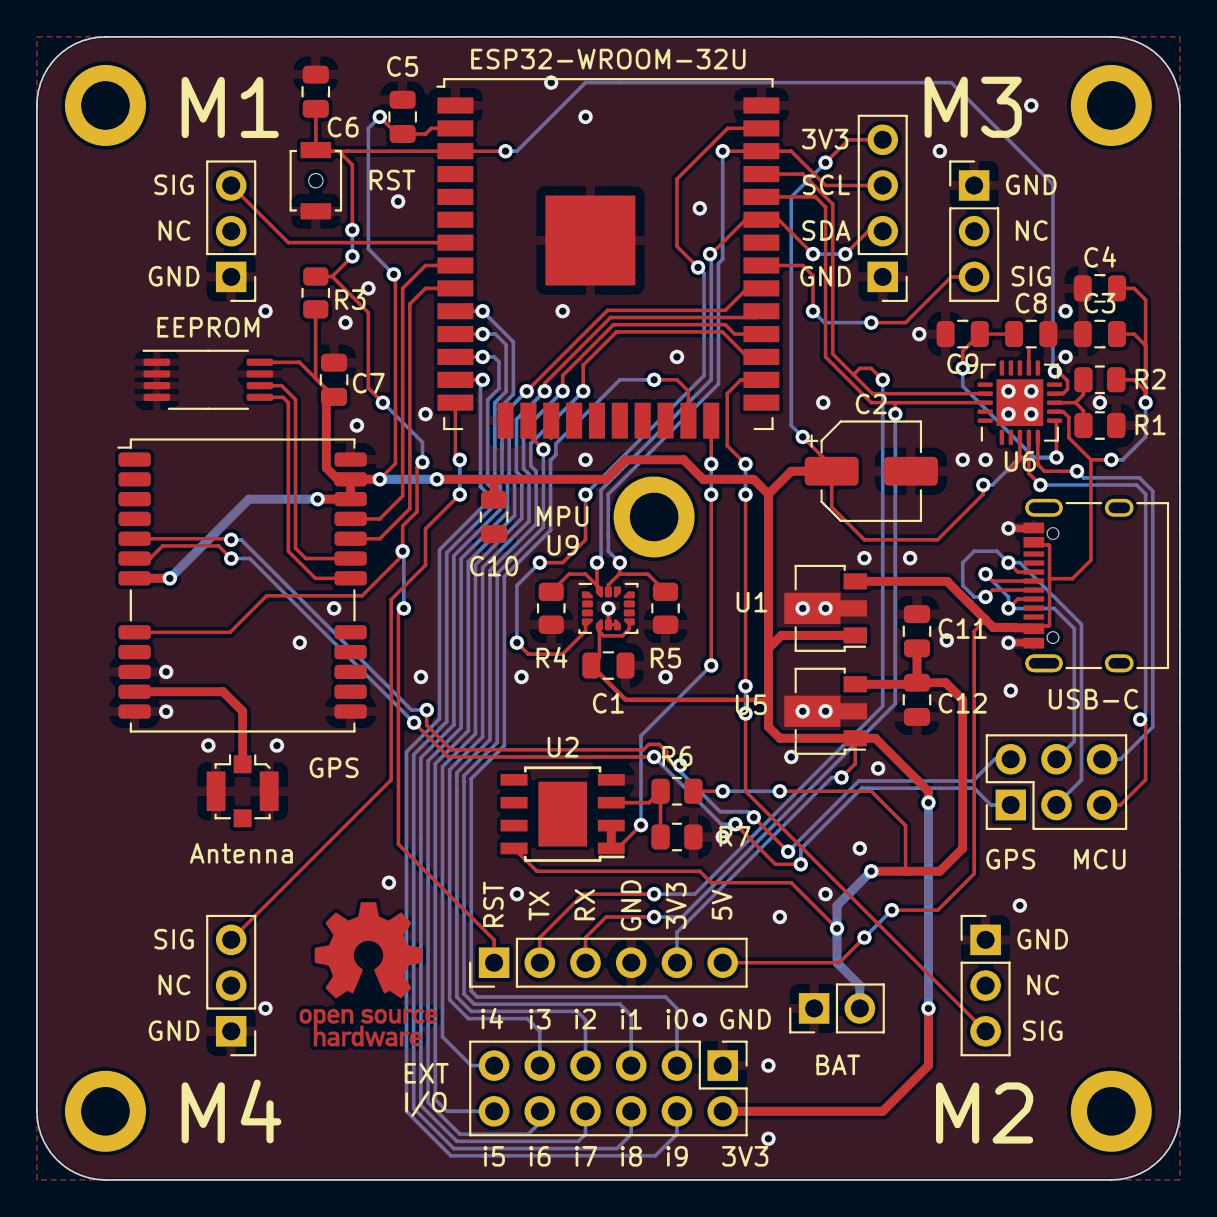
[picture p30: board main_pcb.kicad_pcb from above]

Board: 2 copper layers, 63.5 x 63.5 mm, 39 parts (0 on the bottom side), 38 nets.

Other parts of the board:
Antenna: U.FL; U.FL_Molex_MCRF_73412-0110_Vertical
USB-C: USB_C_Receptacle_XKB_U262-16XN-4BVC11

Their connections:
/gps_antenna: Antenna.1; also elsewhere on the board
GND: Antenna.2, USB-C.A1, USB-C.A12, USB-C.B1, USB-C.B12; also elsewhere on the board
USB5V: USB-C.A4, USB-C.A9, USB-C.B4, USB-C.B9; also elsewhere on the board
USB+: USB-C.A6, USB-C.B6; also elsewhere on the board
USB-: USB-C.A7, USB-C.B7; also elsewhere on the board

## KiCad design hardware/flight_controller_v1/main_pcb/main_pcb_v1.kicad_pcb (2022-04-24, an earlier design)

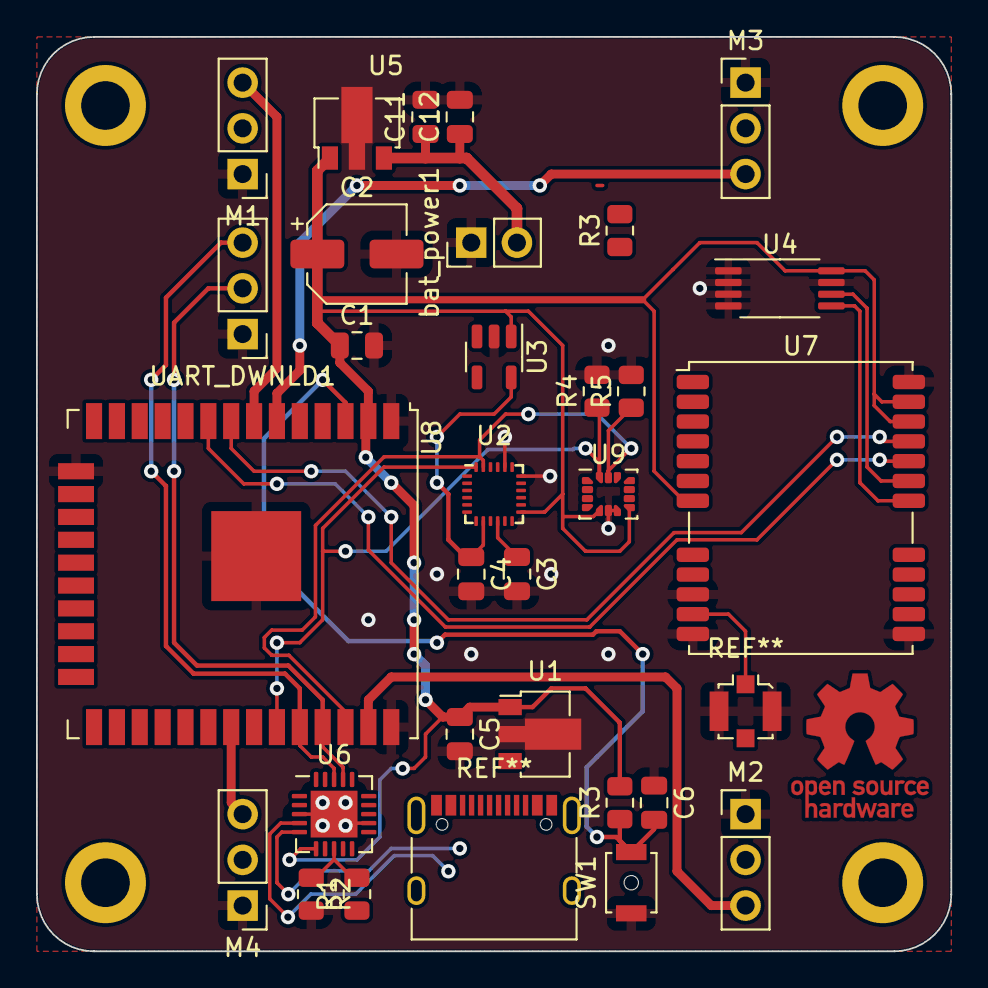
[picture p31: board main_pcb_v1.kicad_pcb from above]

Board: 2 copper layers, 50.8 x 50.8 mm, 30 parts (0 on the bottom side), 19 nets.

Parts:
C1, C3, C4, C5, C12: 0.1uF; C_0805_2012Metric
C2: 10uF; CP_Elec_5x4.5
C6: 1uF; C_0805_2012Metric
C11: 10uF; C_0805_2012Metric
M1, M2, M3, M4: Conn_01x03; PinHeader_1x03_P2.54mm_Vertical
R1: 22.1k; R_0805_2012Metric
R2: 47.5k; R_0805_2012Metric
R3, R4, R5: 10k; R_0805_2012Metric
R3#2: R; R_0805_2012Metric
SW1: SW_Push; SW_SPST_B3U-1000P-B
U1, U5: L78L33_SOT89; SOT-89-3
U2: ICM-20948; InvenSense_QFN-24_3x3mm_P0.4mm
U3: TLV70018_SOT23-5; SOT-23-5
U4: 24LC32; TSSOP-8_4.4x3mm_P0.65mm
U6: CP2102N-Axx-xQFN20; MLF-20-1EP_4x4mm_P0.5mm_EP2.6x2.6mm
U7: NEO-M8N; ublox_NEO
U8: ESP32-WROOM-32U
U9: LSM6DS3; LGA-14_3x2.5mm_P0.5mm_LayoutBorder3x4y
UART_DWNLD1: Conn_01x03; PinHeader_1x03_P2.54mm_Vertical
bat_power1: Conn_01x02; PinHeader_1x02_P2.54mm_Vertical

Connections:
+1V8: C4.1, U2.8 (VDDIO), U3.5 (OUT)
+3V3: C1.1, C2.1, C5.1, R3.2, U1.1 (OUT), U2.13 (VDD), U3.1 (IN), U4.8 (VCC), U5.1 (OUT), U6.6 (VDD), U7.7 (VDD_USB), U7.22 (V_BCKP), U7.23 (VCC), U8.2 (VDD), U9.5 (VDDIO), U9.8 (VDD)
GND: C1.2, C2.2, C3.2, C4.2, C5.2, C6.1, C11.2, C12.2, M1.1, M2.1, M3.1, M4.1, R2.2, R4.2, R5.2, SW1.1, U1.2 (GND), U2.18 (GND), U2.20 (GND), U3.2 (GND), U4.1 (A0), U4.2 (A1), U4.3 (A2), U4.4 (GND), U4.7 (WP), U5.2 (GND), U6.3 (GND), U6.12 (GND), U6.21 (GND), U7.10 (GND), U7.12 (GND), U7.13 (GND), U7.24 (GND), U8.1 (GND), U8.15 (GND), U8.38 (GND), U8.39 (GND), U9.6 (GND), U9.7 (GND), UART_DWNLD1.1, bat_power1.1
GPS_RX: U7.21 (RXD/SPI_MOSI), U8.8 (IO32)
GPS_TX: U7.20 (TXD/SPI_MISO), U8.9 (IO33)
M1: M1.3, U8.7 (IO35)
M2: M2.3, U8.37 (IO23)
M3: M3.3, U8.6 (IO34)
M4: M4.3, U8.31 (IO19)
unnamed: C3.1, U2.10 (REGOUT)
unnamed: R1.2, R2.1, U6.8 (VBUS)
RESET: C6.2, R3.1, SW1.2, U8.3 (EN)
RX: U6.18 (TXD), U8.34 (RXD0/IO3), UART_DWNLD1.3
SCL: R5.1, U2.23 (SCL/SCLK), U8.36 (IO22), U9.13 (SCL)
SCL_eeprom: U4.6 (SCL), U7.19 (SCL/SPI_CLK)
SDA: R4.1, U2.24 (SDA/SDI), U8.33 (IO21), U9.14 (SDA)
SDA_eeprom: U4.5 (SDA), U7.18 (SDA/~SPI_CS)
TX: U6.17 (RXD), U8.35 (TXD0/IO1), UART_DWNLD1.2
v_bat: C11.1, C12.1, U5.3 (IN), bat_power1.2

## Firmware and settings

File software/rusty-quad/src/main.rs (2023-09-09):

#![feature(type_changing_struct_update)]
#![feature(type_alias_impl_trait)]
#![feature(async_fn_in_trait)]
#![no_std]
#![no_main]

use defmt_rtt as _;
use panic_probe as _;
use embassy_futures as _;

use embassy_time::Duration;

const IMU_SAMPLE_TIME: Duration = Duration::from_hz(500);

#[cfg(not(feature = "mag"))]
type ImuData = icm20948_async::Data6Dof;
#[cfg(feature = "mag")]
type ImuData = icm20948_async::Data9Dof;

// Load module for cross-task channels
mod signals;

// Static i2c mutex for shared-bus functionality
use static_cell::StaticCell;
use embassy_sync::mutex::Mutex;
use embassy_sync::blocking_mutex::raw::CriticalSectionRawMutex as CSRMutex;
use embassy_rp::{i2c::{I2c,Async},peripherals::I2C1, gpio::Pin};
static SHARED_ASYNC_I2C : StaticCell<Mutex<CSRMutex, I2c<I2C1, Async>>> = StaticCell::new();

// Import task modules
mod task_blinker;
mod task_attitude_controller;
mod task_motor_governor;
mod task_imu_reader;
mod task_sbus_reader;
mod task_state_estimator;
mod task_commander;
mod task_motor_mixing;
mod task_flight_detector;

// Import misc modules
mod functions;
mod sbus_cmd;
mod imu;

#[embassy_executor::main]
async fn main(spawner: embassy_executor::Spawner) {
    let p = embassy_rp::init(Default::default());

    // Create quad-motor PIO runner
    let quad_pio_motors = {
        use dshot_pio::dshot_embassy_rp::DshotPio;
        use embassy_rp::{pio::*,bind_interrupts,peripherals::PIO0};
        bind_interrupts!(struct Pio0Irqs {PIO0_IRQ_0 => InterruptHandler<PIO0>;});
        DshotPio::<4,_>::new(
            p.PIO0,
            Pio0Irqs,
            p.PIN_13,
            p.PIN_7,
            p.PIN_6,
            p.PIN_12,
            (52, 0)
        )
    };

    // Configure and setup sbus compatible uart RX connection
    let uart_rx_sbus = {
        use embassy_rp::{uart::*,bind_interrupts,peripherals::UART1};
        bind_interrupts!(struct Uart1Irqs {UART1_IRQ => InterruptHandler<UART1>;});
        let mut sbus_uart_config = Config::default();
        sbus_uart_config.baudrate = 100_000;
        sbus_uart_config.data_bits = DataBits::DataBits8;
        sbus_uart_config.stop_bits = StopBits::STOP2;
        sbus_uart_config.parity = Parity::ParityEven;
        sbus_uart_config.invert_rx = true;
        UartRx::new(p.UART1, p.PIN_9,Uart1Irqs, p.DMA_CH0, sbus_uart_config)
    };

    // Configure and setup shared async I2C communication
    let shared_i2c = {
        use embassy_rp::{i2c,bind_interrupts};
        bind_interrupts!(struct I2c1Irqs {I2C1_IRQ => i2c::InterruptHandler<I2C1>;});
        let mut i2c_config = i2c::Config::default();
        i2c_config.frequency = 400_000; // High speed i2c
        let i2c = I2c::new_async(p.I2C1, p.PIN_11, p.PIN_10, I2c1Irqs, i2c_config);
        SHARED_ASYNC_I2C.init(Mutex::new(i2c))
    };

    // Share async i2c bus
    use embassy_embedded_hal::shared_bus::asynch::i2c::I2cDevice;
    let i2c_bus_imu = I2cDevice::new(shared_i2c);

    // Spawning of system tasks

    use crate::task_commander::commander;
    spawner.must_spawn(commander(
        signals::SBUS_CMD.subscriber().unwrap(), 
        signals::MOTOR_STATE.subscriber().unwrap(),
        signals::ATTITUDE_SENSE.subscriber().unwrap(), 
        signals::FLIGHT_MODE.subscriber().unwrap(),
        signals::MOTOR_ARM.publisher().unwrap(), 
        signals::MOTOR_DIR.publisher().unwrap(),
        signals::THRUST_ACTUATE.publisher().unwrap(),
        signals::BLINKER_MODE.publisher().unwrap(),
        signals::ATTITUDE_INT_RESET.publisher().unwrap(),
        signals::ATTITUDE_STAB_MODE.publisher().unwrap(),
    ));

    use crate::task_sbus_reader::sbus_reader;
    spawner.must_spawn(sbus_reader(
        uart_rx_sbus,
        signals::SBUS_CMD.publisher().unwrap(),
        Duration::from_millis(500),
    ));

    use crate::task_imu_reader::imu_reader;
    spawner.must_spawn(imu_reader(
        i2c_bus_imu,
        signals::IMU_READING.publisher().unwrap(),
        IMU_SAMPLE_TIME
    ));

    use crate::task_state_estimator::state_estimator;
    spawner.must_spawn(state_estimator(
        signals::IMU_READING.subscriber().unwrap(), 
        signals::ATTITUDE_SENSE.publisher().unwrap(), 
        IMU_SAMPLE_TIME
    ));

    use crate::task_attitude_controller::attitude_controller;
    spawner.must_spawn(attitude_controller(
        signals::ATTITUDE_SENSE.subscriber().unwrap(),
        signals::ATTITUDE_INT_RESET.subscriber().unwrap(),
        signals::ATTITUDE_STAB_MODE.subscriber().unwrap(),
        signals::ATTITUDE_ACTUATE.publisher().unwrap(),
        IMU_SAMPLE_TIME
    ));

    use crate::task_motor_mixing::motor_mixing;
    spawner.must_spawn(motor_mixing(
        signals::THRUST_ACTUATE.subscriber().unwrap(),
        signals::ATTITUDE_ACTUATE.subscriber().unwrap(),
        signals::MOTOR_ARM.subscriber().unwrap(),
        signals::MOTOR_SPEED.publisher().unwrap(),
    ));

    use crate::task_motor_governor::motor_governor;
    spawner.must_spawn(motor_governor(
        signals::MOTOR_SPEED.subscriber().unwrap(),
        signals::MOTOR_DIR.subscriber().unwrap(),
        signals::MOTOR_STATE.publisher().unwrap(),
        quad_pio_motors,
        Duration::from_millis(100),
    ));

    use crate::task_blinker::blinker;
    spawner.must_spawn(blinker(
        signals::BLINKER_MODE.subscriber().unwrap(),
        p.PIN_25.degrade()
    ));

    use crate::task_flight_detector::flight_detector;
    spawner.must_spawn(flight_detector(
        signals::MOTOR_STATE.subscriber().unwrap(),
        signals::FLIGHT_MODE.publisher().unwrap(),
    ));

    // Ensure all signal subscribers are used
    assert!(signals::IMU_READING.subscriber().is_err());
    assert!(signals::ATTITUDE_SENSE.subscriber().is_err());
    assert!(signals::ATTITUDE_ACTUATE.subscriber().is_err());
    assert!(signals::ATTITUDE_INT_RESET.subscriber().is_err());
    assert!(signals::ATTITUDE_STAB_MODE.subscriber().is_err());
    assert!(signals::MOTOR_SPEED.subscriber().is_err());
    assert!(signals::MOTOR_ARM.subscriber().is_err());
    assert!(signals::MOTOR_DIR.subscriber().is_err());
    assert!(signals::MOTOR_STATE.subscriber().is_err());
    assert!(signals::SBUS_CMD.subscriber().is_err());
    assert!(signals::THRUST_ACTUATE.subscriber().is_err());
    assert!(signals::BLINKER_MODE.subscriber().is_err());

}

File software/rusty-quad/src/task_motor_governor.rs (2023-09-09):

use defmt::{info, warn, Format};
use embassy_rp::peripherals::PIO0;
use embassy_time::{Duration, Timer, with_timeout};
use dshot_pio::{dshot_embassy_rp::DshotPio, DshotPioTrait};
use crate::signals;

static TASK_ID : &str = "MOTOR_GOVERNOR";

/// Task to govern the arming, disarming and speed settings of the motors.
/// Arming takes 3.5 seconds: 3.0 s to arm, 0.5 s to set direction
#[embassy_executor::task]
pub async fn motor_governor(
    mut in_sg_motor_speed: signals::MotorSpeedSub,
    mut in_sg_motor_dir: signals::MotorDirSub,
    out_sg_motor_arm_state: signals::MotorStatePub,
    mut out_quad_pio_motors: DshotPio<'static,4,PIO0>,
    cfg_timeout_receive: Duration,
) {

    let mut cfg_reverse_motor = in_sg_motor_dir.next_message_pure().await;

    out_sg_motor_arm_state.publish_immediate(MotorState::Disarmed(DisarmReason::NotInitialized));

    loop {
        // Wait for signal to arm motors
        while in_sg_motor_speed.next_message_pure().await.is_none() {}

        // Check if motor direction has been configured
        if let Some(r) = in_sg_motor_dir.try_next_message_pure() {cfg_reverse_motor = r}

        // Send minimum throttle for a few seconds to arm the ESCs
        info!("{} : Initializing motors",TASK_ID);
        Timer::after(Duration::from_millis(500)).await;
        for _i in 0..50 {
            out_quad_pio_motors.throttle_minimum();
            Timer::after(Duration::from_millis(50)).await;
        }

        // Set motor directions for the four motors
        info!("{} : Setting motor directions",TASK_ID);
        for _i in 0..10 {
            out_quad_pio_motors.reverse(cfg_reverse_motor.into());
            Timer::after(Duration::from_millis(50)).await;
        }

        // Set motors armed signal
        out_sg_motor_arm_state.publish_immediate(MotorState::Armed(ArmedState::Idle));

        info!("{} : Entering main loop",TASK_ID);
        loop {

            match with_timeout(cfg_timeout_receive, in_sg_motor_speed.next_message_pure()).await {

                // Motor speed message received correctly
                Ok(Some(speeds)) => {
                    out_quad_pio_motors.throttle_clamp(speeds.into());
                    out_sg_motor_arm_state.publish_immediate(MotorState::Armed(ArmedState::Running(speeds)));
                },

                // Channel commanded motors to disarm
                Ok(None) =>  {
                    warn!("{} : Disarming motors -> commanded",TASK_ID);
                    out_quad_pio_motors.throttle_minimum();
                    out_sg_motor_arm_state.publish_immediate(MotorState::Disarmed(DisarmReason::Commanded));
                    break
                },

                // Automatic disarm due to message timeout
                Err(_) =>  {
                    warn!("{} : Disarming motors -> timeout",TASK_ID);
                    out_quad_pio_motors.throttle_minimum();
                    out_sg_motor_arm_state.publish_immediate(MotorState::Disarmed(DisarmReason::Timeout));
                    break
                }
            }
        }
    }
}

#[derive(Clone,Copy,Format,PartialEq)]
pub enum MotorState {
    Disarmed(DisarmReason),
    Armed(ArmedState)
}

#[derive(Clone,Copy,Format,PartialEq)]
pub enum ArmedState {
    Running((u16,u16,u16,u16)),
    Idle
}

#[derive(Clone,Copy,Format,PartialEq)]
pub enum DisarmReason{
    NotInitialized,
    Commanded,
    Timeout
}

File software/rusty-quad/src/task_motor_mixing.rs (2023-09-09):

use defmt::*;
use embassy_futures::select::{select, Either};

use crate::task_attitude_controller::Attitude;
use crate::signals;

static TASK_ID : &str = "MOTOR_MIXING";

#[embassy_executor::task]
pub async fn motor_mixing(
    mut in_sg_thrust_cmd: signals::ThrustActuateSub,
    mut in_sg_attitude_cmd: signals::AttitudeActuateSub,
    mut in_sg_motor_arm: signals::MotorArmSub,
    out_sg_motor_speed: signals::MotorSpeedPub,
) {

    let mut arm_motors = false;

    let mut attitude = Attitude::new(0., 0., 0.);
    let mut thrust = 0.0;

    info!("{} : Entering main loop",TASK_ID);
    loop {

        match select(in_sg_attitude_cmd.next_message_pure(), in_sg_thrust_cmd.next_message_pure()).await {
            Either::First(a) => attitude = a,
            Either::Second(t) => thrust = t,
        }

        let command = motor_mixing_matrix(thrust, attitude.pitch, attitude.roll, attitude.yaw, 70., 2047.);

        if let Some(arm) = in_sg_motor_arm.try_next_message_pure() {
            arm_motors = arm
        }

        match arm_motors {
            true => out_sg_motor_speed.publish_immediate(Some(command)),
            false => out_sg_motor_speed.publish_immediate(None)
        }

    }
}

/// Basic quad-copter motor mixing function
fn motor_mixing_matrix(thrust: f32, pitch: f32, roll: f32, yaw: f32, min: f32, max: f32) -> (u16,u16,u16,u16) {
    (
        (thrust + pitch + roll + yaw).clamp(min, max) as u16,
        (thrust - pitch - roll + yaw).clamp(min, max) as u16,
        (thrust + pitch - roll - yaw).clamp(min, max) as u16,
        (thrust - pitch + roll - yaw).clamp(min, max) as u16,
    )
}

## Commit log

2021-12-21 Added initial firmware and 3D models
    [droneframe_pcb_clamp.obj, droneframe_pcb_clamp.step]
2021-12-21 Added sigProc library with PID controller
2022-01-25 Updated ESP32 software to support flight and ground programs, added initial python ground software
    [11cm_spacer.FCStd, 11cm_spacer.obj, pitch_bearing_pivot.obj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]
2022-02-14 Added 3D model for thrust test stand
    [thrust_mount.FCStd, thrust_mount_bottom.obj, thrust_mount_top.obj]
2022-02-15 Tested and documented determination of thrust time constant
    [0500_thrust_response.csv, 1200_thrust_response.csv, 1500_thrust_response.csv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]
2022-02-15 Added tools for thrust step documentation
2022-02-15 Small changes to thrust test doc
2022-02-18 Updated motor governing code, added few 3D models
    [droneframe_pcb_clamp_insert.obj, landing_gear.obj]
2022-02-27 Additional tests and documentation added for motor model and roll/pitch equations of motion
2022-03-01 Added 32 cm spacers for wider drone test stand
    [32cm_spacer_pair.FCStd, 32cm_spacer_pair.obj]
2022-03-12 Added extra 3D parts for 32 cm test stand
    [32cm_spacer_pair.FCStd, swivel_point_32cm.FCStd, swivel_point_32cm.obj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]
2022-03-13 Added test and documentation for roll moment of inertia
    [inertia_left_point.csv, inertia_right_point.csv, pitch_bearing_pivot_wide.obj]
2022-03-13 Added optional output limiter to PID controller
2022-03-13 Added anti-windup to PID integrator
2022-04-21 Added initial kicad main-pcb
    [main_pcb.kicad_pcb, main_pcb.kicad_sch]
2022-04-21 Slight changes to PCB
    [main_pcb.kicad_pcb, main_pcb.kicad_sch]
2022-04-24 Major changes to main code structure. More modularity incoming
    [configuration.h]
2022-04-24 New PCB iteration
    [main_pcb.kicad_pcb, main_pcb.kicad_sch, main_pcb_v1.kicad_pcb]
2022-04-24 Added gerber files for current version of PCB
    [main_pcb-B_Cu.gbr, main_pcb-B_Mask.gbr, main_pcb-B_Paste.gbr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]
2022-04-30 Code restructure
    [configuration.h]
2022-05-08 Update main flight code
    [configuration.h]
2022-05-08 Added firmware for gathering data
    [configuration.h]
2022-05-08 Added test data for kalman filter test
    [kalman_fastdrive.csv, kalman_linear_drive.csv, kalman_parkinlot_drive1.csv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]
2022-08-08 Code restructuring in progress..
    [MPU6050_noise.csv, configuration.h, droneframe_main_v1.1_propguard.obj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]
2022-08-09 Updated readmes, removed old files and updates some folder structures
    [0500_thrust_response.csv, 1200_thrust_response.csv, 1500_thrust_response.csv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]
2022-08-20 Added Functional Kalman filter implementation in Python
2022-08-27 Update kalman filtering python code
2022-12-07 Mega update to fligth firmware
    [configuration.h]
2023-03-15 Added initial Rusty flight controller
    [configuration.h]
2023-03-29 Match different switch C positions to throttle profile
2023-04-11 Fixed issue causing yaw wrapping to not work as intended
    [main.rs]
2023-04-13 Add stl for legs and battery holder
2023-04-23 Moved from Matlab to Julia for processing of test data (inertia)
    [pitch_inertia_left_point.csv, pitch_inertia_right_point.csv]
2023-04-25 Restructure. All tasks are moved to seperate modules. Added shared i2c-bus support.
2023-04-25 Moved hard-coded motor directions into main file
2023-07-02 Added magnetometer feature flag to flight controller. Uses updated quad-dshot-pio crate
2023-07-06 WIP starting framework for shared IMU traits
2023-09-09 Added document describing idea behind current firmware architechture
